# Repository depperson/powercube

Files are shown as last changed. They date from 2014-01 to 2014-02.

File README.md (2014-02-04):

Power Cube
=========

The Power Cube is a modular, universal, self-contained power unit consisting of an engine coupled to a hydraulic pump, providing power from hydraulic fluid at high pressure through quick connect hoses. It is designed to function as a modular and interchangeable power supply for GVCS and other open source technologies.

http://opensourceecology.org/wiki/Power_cube

My goal is to package up all of the necessary documentation to build the Power Cube Version 6.

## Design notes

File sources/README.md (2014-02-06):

Power Cube - Sources
=========

These materials related to the Power Cube were collected from the OSE wiki as a forking point for the project. The version at the time of inclusion was PowerCubeV6. Here are some of the URLs for these files. 

http://opensourceecology.org/wiki/Power_cube

http://opensourceecology.org/wiki/Power_Cube_6/Bill_of_Materials

http://opensourceecology.org/wiki/Power_Cube_6/Manufacturing_Instructions

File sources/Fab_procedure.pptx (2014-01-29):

## 1. Cut Steel

- Tubes, 2 ea: 1/4” x 6” x 12” x 26” long
- Angle iron, 10 ea: 27” per frame diagram
- Angle iron 1/4” x 2” x 2”, 2 ea: 4”, 1 ea: 2”, 2 ea: 8”
- Flat steel, 1/4” x 6”: 1 ea: 6”, 4 ea: 12”
- Flat steel, 1/4” x 8”: 13.5”
- Flat steel 1/8” x 4”: 1 ea: 14”, 2 ea: 1”
- 1 ½" x 2” pipe coupling: cut in half
- 1” engine shaft: cut in half
- 3/4” 11 tooth spline shaft: cut in half

## 2. Fabricate tanks

- Torch, then grind tubes and end plates
- Drill ½” holes for sight gauge
- Install sight gauge
- Weld flanges, pipe coupling and filler neck
- Weld end plates on tanks
- Weld supports for engine & control panel
- Weld battery bracket to fuel tank and solenoid bracket to battery bracket
- Soap bubble test and re-weld if necessary
- Drill smaller 7/16” holes & tap ¼” NPTF
- Mask holes and paint

## 3. Shaft Coupling

- Cut couplings in half
- Preferably: Use lathe to turn down cut ends
- Insert plug into coupling halves
- Clamp and weld
- Let cool standing vertically
- Paint external surfaces

## 4. Weld Frame

- Note: Mitered joints welded on inside and outside
- Begin in one corner, lay two members on flat surface, clamp and weld
- Add third member, clamp and measure – verify parallel with opposing member and weld
- Add forth member, verify alignment and weld
- Complete second rectangle
- Weld hoist points to upper frame members
- Align fifth and sixth members on one rectangle and weld
- Align second rectangle to first, position tanks inside frame and complete frame welds
- Weld expanded steel to hydraulic reservoir
- Weld solenoid bracket to battery bracket
- Paint frame & tank surfaces that will be inaccessible later
- Weld tanks to frame

## 5. Engine/pump mount

- Torch & drill holes in engine & pump plates – verify that holes on engine plate match those on support brackets on tanks
- Weld angle iron to pump plate
- Mount pump on pump plate
- Mount engine on engine plate
- Insert key in shaft coupling and connect to engine
- Slide pump assembly to shaft coupling
- Place 4” spacers between pump & engine plates
- Tack angle iron to engine plate
- Remove spacers and weld
- Remove engine / pump assembly and paint

## 6. Fabricate Control Panel

- Torch, drill, file control panel holes to drawing
- For key switch hole, use switch while filing to test for proper hole size
- Weld throttle bracket to back side & drill bracket
- Paint
- Mount control panel components:
  - Quick couplers
  - Key switch
  - Throttle

## 7. Fabricate Wire Harness

- Cut wire:
  - 2 ea: 10” 2 ga red
  - 1 ea: 12” 2 ga black
- 3/8” copper tubing: 6 ea @ 1 ½”
- Align wires, cut and strip ends appropriately
- Crimp fan connectors on wires
- Crimp circular lug on wire for solenoid
- Crimp pins on wires and insert into connector
- On large gauge wires, begin on ends with single wire – flare ends of copper tubing, insert wire, flatten with hammer and drill
- Proceed to ends with multiple wires – flare, insert, flatten and drill
- Cut heat shrink tubing, install on cables with multiple wires and heat to shrink

## 8. Oil Cooler & Fan

- Put teflon tape onto elbow connector NPT threads
- Screw elbows into oil cooler
- Position oil cooler: elbows up and facing you
- Insert plastic brackets in fan
- Place fan on oil cooler – wires pointing left
- Insert plastic fasteners through oil cooler and plastic fasteners, then secure (use foam pads to protect fins)

## 9. Install Engine / Pump

- Hoist engine / pump
- Attach vibration isolators to supports on tanks – loosely tighten from underneath
- Lower engine into frame until mated with isolators
- With full weight on vibration isolators install and tighten nuts

## 10. Install Oil Cooler & Fan

- Slide oil cooler / fan in place – be careful not to damage cooler fins
- Loosely connect hydraulic hoses to oil cooler elbows
- Test alignment of hydraulic hoses and adjust elbows if necessary
- Install oil cooler/fan to expanded steel using rubber bushings and bolts

## 11. Install Control Panel

- Position control panel
- Connect and tighten hydraulic hoses between oil cooler and control panel
- Connect ¼” hose for “Tank Return” to control panel and tank using hose clamps

## 12. Wire Harness and Battery

- Mount solenoid to bracket
- Insert battery in place
- Plug key switch connector to switch
- Plug in fan connectors
- Connect wire lug to solenoid
- Connect black battery cable to engine bolt and to battery
- Connect red cable to solenoid and engine
- Connect red cable to solenoid, then battery

## 13. Install Suction Plumbing

- Use teflon tape on all NTP threads!
- Install tank strainer in tank
- Install 1” x 4” nipple in strainer
- Install 1” elbow on nipple
- Install suction hose with 2 ea hose clamps

## 14. Install Supply Plumbing

- Use Teflon tape on all NPT threads!
- Connect “long” elbow to pump
- Connect ½” 1' hose between pump elbow and quick connect on control panel – minimize stress on hose
- Install ¾” nipple and filter head to tank – make sure fluid flow is into tank
- Install ¾” elbow in filter head
- Install filter on filter head
- Connect and tighten all ¾” JIC fittings

## 15. Fill With Fluids

## 16.Test

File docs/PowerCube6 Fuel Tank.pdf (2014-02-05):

2/4/2014 | PowerCube6 Fuel Tank - Open Source Ecology
http://opensourceecology.org/wiki/PowerCube6_Fuel_Tank | 1/2

# PowerCube6 Fuel Tank

From Open Source Ecology

Procedure for fabricating the fuel tank. Note that the preparation of the edges for welding is critical, as the welded seams must prevent fuel leaks.

Part List:

Rectangular tube: 1/4" x 6" x 12" - 26" long [2] Flat Steel: 1/4" x 6" x 12"Weld-in Fuel Filler Neck and Cap Smallsheet plastic Fuel Pickup Adapter 1/4" rubber hose Soapy water

1. Grind the 1/4" x 6" x 12" plates, rounding the corners to 1/2" radius and beveling the edges for welding.
2. Grind the 1/2" x 6" x 12" Tube, beveling the edges for welding.
3. Cut the 7/16" and 2" holes in the tube as shown. The larger hole may be cut with an Oxy/Acetylene torch, then smoothed with a grinder. Note that the inside of the hole should be 2" in diameter.
4. Weld the plates to the ends of the tube
5. Tap the 7/16" hole for 1/4" NPTF threads, smooth the welds with the grinder.
6. Pressure test the tank by covering the filler neck with a plastic sheet, then securing the cap. Secure the smaller hole with a the fuel pickup and some 1/4" hose on the hose barb. Apply compressed air to the end of the rubber hose to pressurize the tank, then apply soapy water to all welds and check for bubbles.
7. Mark any bubbling spots with a felt-tip marker and re-weld
8. Re-test the tank and re-weld as necessary to stop all leaks

2/4/2014 | PowerCube6 Fuel Tank - Open Source Ecology

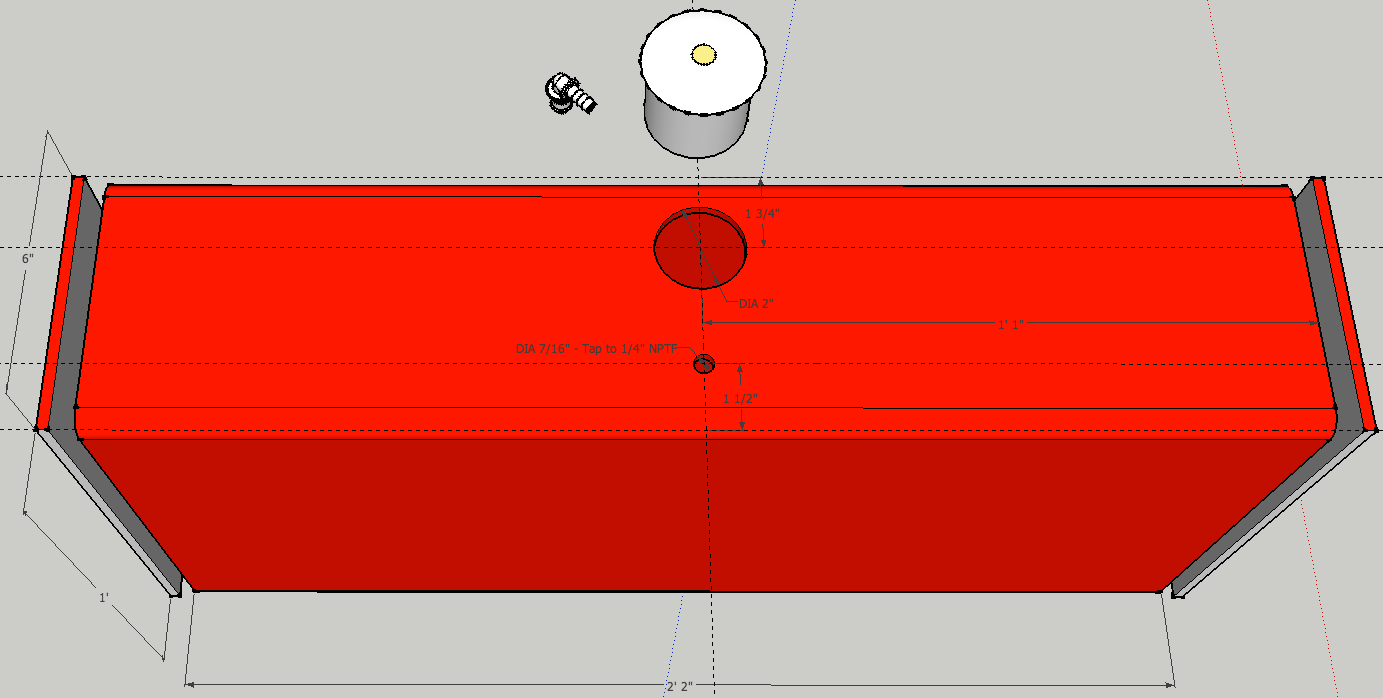
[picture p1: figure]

http://opensourceecology.org/wiki/PowerCube6_Fuel_Tank | 2/2

Retrieved from "http://opensourceecology.org/w/index.php?title=PowerCube6_Fuel_Tank&oldid=71505"

This page was last modified on 21 August 2012, at 02:56.
Content is available under CreativeCommons by-sa3.0. (http://opensourceecology.org/wiki/Copyright)

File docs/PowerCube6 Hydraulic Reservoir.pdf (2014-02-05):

2/4/2014 | PowerCube6 Hydraulic Reservoir - Open Source Ecology
http://opensourceecology.org/wiki/PowerCube6_Hydraulic_Reservoir | 1/2

# PowerCube6 Hydraulic Reservoir

From Open Source Ecology

Procedure for fabricating the hydraulic reservoir. Note that the preparation of the edges for welding is critical, as the welded seams must prevent fluid leaks.

Part List:

1/4" x 6" x 12" - 26"Rectangular tube
[2] 1/4" x 6" x 12" Flat Steel
[2] 3/4" NPTF weld-in flange
3/4" NPTM plastic tank breather
1 1/2" NPTF x 3" union
Hydraulic tank thermometer and sight gauge
[2] 1/4" NPTM plug - Galvanized
[2] 3/4" NPTM plug - PVC
1 1/2" NPTM plug - PVC
Schrader air valve
Soapy water

Procedure:

1. Grind the 1/4" x 6" x 12" plates, rounding the corners to 1/2" radius and beveling the edges for welding.
2. Grind the 1/2" x 6" x 12" Tube, beveling the edges for welding.
3. Cut the 7/16", 1 7/16" and 2" holes in the tube as shown. The larger holes may be cut with an Oxy/Acetylene torch, then smoothed with a grinder.
4. Tap threads in the two smaller holes with a 1/4" NPTF tap
5. Weld the three flanges to the tank
6. Weld the "front" plate (ie: the one near the oilfilter) to the end of the tube
7. Drill the two 1/2" holes for site gauge and securely install the site gauge
8. Tap the 7/16" hole for 1/4" NPTF threads, smooth the welds with the grinder.
9. Pressure test the tank by covering the filler neck with a plastic sheet, then securing the cap. Secure the smaller hole with a the fuel pickup and some 1/4" hose on the hose barb. Apply compressed air to the end of the rubber hose to pressurize the tank, then apply soapy water to all welds and check for bubbles.
10. Mark any bubbling spots with a felt-tip marker and re-weld
11. Re-test the tank and re-weld as necessary to stop all leaks

2/4/2014 | PowerCube6 Hydraulic Reservoir - Open Source Ecology

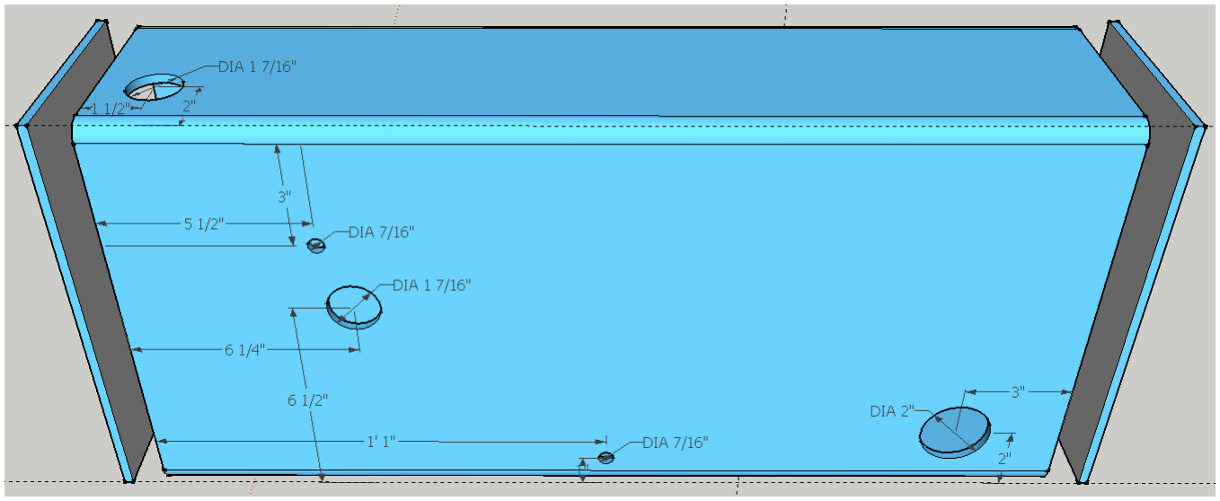
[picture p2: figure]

http://opensourceecology.org/wiki/PowerCube6_Hydraulic_Reservoir | 2/2

Retrieved from "http://opensourceecology.org/w/index.php?title=PowerCube6_Hydraulic_Reservoir&oldid=71588"

This page was last modified on 22 August 2012, at 14:56.
Content is available under CreativeCommons by-sa3.0. (http://opensourceecology.org/wiki/Copyright)

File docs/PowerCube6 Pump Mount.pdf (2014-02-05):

2/4/2014 | PowerCube6 Pump Mount - Open Source Ecology

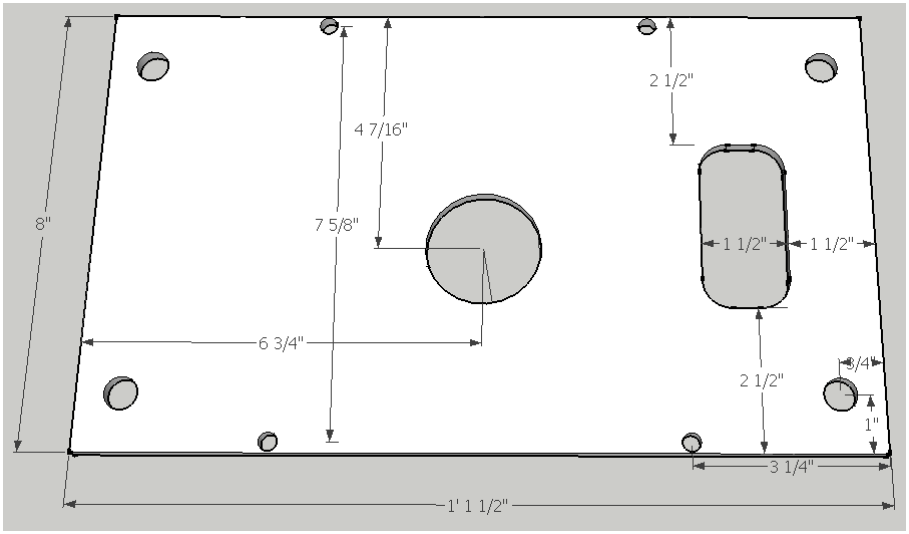
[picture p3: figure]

http://opensourceecology.org/wiki/PowerCube6_Pump_Mount | 1/5

# PowerCube6 Pump Mount

From Open Source Ecology

## Engine Mounting Plates

¼” x 8” x 13.5” Plate

¼” x 6” x 6” Plate

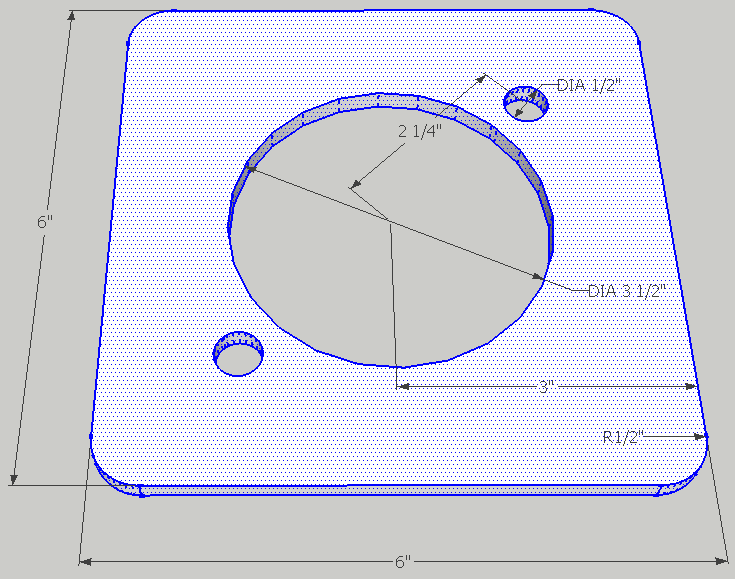
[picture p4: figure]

¼” x 2” x 2” x 5” Angle (2 ea)

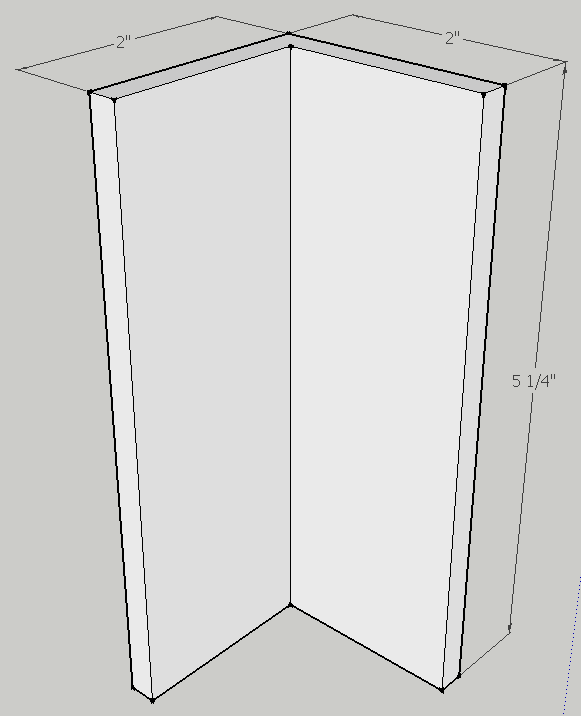
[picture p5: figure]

## Engine / Pump Mount Assembly

Align the two 1/4" x 2" x 2" anglt iron pieces on the pump plate as shown below and weld securely.

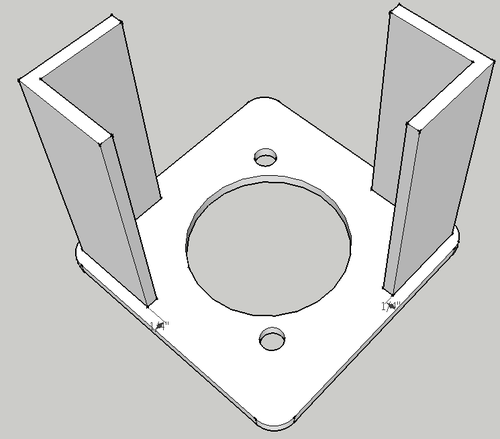
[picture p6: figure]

Mount the engine to the engine plate using [4] 5/16” x 2” bolts and [4] rubber vibration mounts.

Slide the shaft coupling onto the engine shaft and secure the hex screw.

Mount the pump onto the pump plate and secure with [2] 7/16" x 1 1/2" bolts.

Slide the splined pump shaft into the shaft coupling so the angle touches the engine plate and is oriented as shown.

See the following video for details:

Examine the engine shaft – it should be 2” long. If longer, cut the shaft to extend no more than 2” from the case. This length is necessary for the coupling. Put the larger keystock in the engine shaft and slide the shaft coupling on the engine shaft and tighten the allen screws to hold it in place.

Retrieved from "http://opensourceecology.org/w/index.php?title=PowerCube6_Pump_Mount&oldid=71278"

This page was last modified on 18 August 2012, at 06:29.
Content is available under CreativeCommons by-sa3.0. (http://opensourceecology.org/wiki/Copyright)

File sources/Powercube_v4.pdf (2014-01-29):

Power Cube | Open Source Ecology | Page 1

# Power Cube

Version 4

Contents

## Table of Contents

Introduction

The Power Cube is an universal, self-contained power unit that consists of an engine coupled to a hydraulic pump for providing power in the form of hydraulic fluid at high pressure. It connects via quick couplers and quick-connect hydraulic hoses to devices such as:

- LifeTrac
- CEB Press
- Sawmill

◦

This document provides information for building and using a Power Cube as part of the Open Source Ecology (OSE) project.

Check the OSE website for updates to this document:

http://opensourceecology.org/wiki/File:Powercube.odt

Bill Of Materials

Discrete parts

Name | Qty | Dimensions | Manufacturer /
Retailer | Part No.
Engine | 1 | 28 HP | Briggs & Stratton | 49M777 Series
Solid Shaft Coupling | 1 | 1 1/8” x 5/8” | Sweiger Shop | Custom
Hydraulic Pump | 1 | 0.976 cu in | SurplusCenter.com | 9-1766-B
SAE 10M x 3/4” NPTF Adapter | 1 | 3/4” NPTM | SurplusCenter.com | 9-6405-10-12
3/4" NPTF Return Filter & Head | 1 | 20 GPM | SurplusCenter.com | 9-059
14 GPM Hydraulic Tank Strainer | 1 | 1 1/2” F x 1” M SurplusCenter.com | 9-7290-100
3/4" NPTM TO 3/4" NPTM 90
Elbow | 1 | ¾” | SurplusCenter.com | 9-5500-10-12
JIC 12M x 3/4 NPTM 90 ELBOW | 1 | 12M x 3/4” | SurplusCenter.com | 9-2501-12-12
3/4" Quick Coupler S40-6 F/F | 1 | 3/4” | SurplusCenter.com | 928-C
1/4" NPT Quick Coupler S40-2 | 1 | 1/4” | SurplusCenter.com | 9-6314
1/4 NPTM TO 3/4 NPTF
ADAPTER | 1 | 1/4” x 3/4” NPT SurplusCenter.com | 9-5405-12
NPT Weld-In Tank Flange | 1 | 1 1/2” | SurplusCenter.com | 9-7843-24
NPT Weld-In Tank Flange | 2 | 3/4” | SurplusCenter.com | 9-7843-12
NPT Weld-In Tank Flange | 1 | ¼” | SurplusCenter.com | 9-7843-4
Hose barb | 1 | ¼" NPTM x 1/4" SurplusCenter.com | 455-AA
1" Hose Barb to SAE 12M
Adapter | 1 | 1” Hose x SAE
| | 12M | SurplusCenter.com | 9-4604-16-12
1" Hose Barb to 1" NPTM
Adapter | 1 | 1” x 1” NPTM SurplusCenter.com | 9-4404-16-16
Hydraulic Suction Hose | 1 | 3' | SurplusCenter.com | 9-1279
Hydraulic Oil Cooler | 1 | Approx 12” x 15” SweigerShop.com | Custom
JIC 12F X JIC 12F 3000 PSI
HYD HOSE | 1 | 3/4” x 12” | SurplusCenter.com | 951-2212
3/4" NPT PLASTIC TANK
BREATHER | 1 | 3/4” | SurplusCenter.com | 9-7957-12
3/4" X 3/4" X 3/4" NPTF TEE | 1 | 3/4" x 3/4" x 3/4" SurplusCenter.com | 9-5605-12-12-12
3/4" NPT HEX NIPPLE | 4 | 3/4” | SurplusCenter.com | 9-5404-12-12
JIC 12M x 3/4" NPTM 90 Elbow | 1 | 3/4” | SurplusCenter.com | 9-2501-12-12

Name | Qty | Dimensions | Manufacturer /
| | | Retailer | Part No.
JIC 12M x JIC 12M UNION | 1 | JIM 12M | SurplusCenter.com | 9-2404-12-12
Solenoid | 1 | | SurplusCenter.com | 11-1108
12 Volt radiator fan | 1 | 12” - 14” | Auto Part
Rubber Fuel Line | 1 | 24” | Auto Part
Battery | 1 | 5" x 7.5" x 7.5" Walmart | UIP-7
Galvanized Nipple | 4 | 1” | Home Depot | 64310
Galvanized Elbow | 2 | 1” | Home Depot | 510-003HN
Galvanized Washer | 4 | 2 ½” | ?? | ??
Galvanized Round | 2 | 2” | ?? | ??
Teflon Tape | 1 roll | ½” wide | Home Depot | ??
1 Gauge Wire | 30” | 1 gauge | Auto Part | ??
1 gauge ring connector
- or -
Copper tubing | 6
- or -
| 9” | 1 gauge
- or -
| | 3/8” | Auto Part | ??
Ignition Switch | 1
12 V Fan Switch | 1
Bolt (Angle iron attach) | 4 | ½” x 2” x 12 TPI
Nut (Angle iron attach) | 4 | ½” x 12 TPI
Washer flat | 8 | ½”
Bolt (Engine mount) | 4 | ¼” x 2” 16 TPI
Nut (Engine mount) | 4 | ¼” x 16 TPI
Bolt (Hydraulic motor mount) | 4 | ¾” x 3.5” x 12 TPI
Nut (Hydraulic motor mount) | 8 | ¾” 12 TPI
Lock washer (Hydraulic motor mount) | 4 | ¾”
Nut (Fan mount) | 4
Bolt (Fan mount) | 4
Bolt (Solenoid mount) | 2
Tractor Enamel: Glossy Black | 1 | pint

Steel
Type | Thickness | Width | Total Length (rounded up)
Angle | ¼" | 2" x 2” 408" (34 ft)
Angle | 1/8” | 2” x 2” 6”
Plate | ¼" | 8" | 38" (4ft)

Plate | ¼” | 2” | 120” (10 ft)
Plate | ¼" | 6" | 24" (2 ft)
Plate | 3/8” | 4” | 54” (5 ft)
Tube | ¼” | 4” x 8” 14 ½” (2 ft)
Tube | ¼” | 6” x 12” 27 ½” (Hydraulic reservoir)
Tube | 1/8” | 4” | 2” | (black pipe)
Tube | 1/8” | 1 9/16” 12” | (Galvanized Muffler Pipe)
Tube | 1/8” | 6 cm | 14” | (Galvanized Muffler Pipe)
Expanded Steel | 13 gauge | 12” | 22” | (Oil cooler grill)

Subassembly Fabrication
Many of the items listed in the Bill Of Materials require preparation before use in assembly of the Power Cube. This includes drilling and cutting steel up to 3/8” in thickness. These are the parts for assembling a Power Cube. Parts without special detail are not illustrated.
1. Engine and Hydraulic Pump mounts
a) ¼” x 8” x 12” Plate
b) ¼” x 8” x 9” Plate
c) ¼” x 2” x 2” x 8” Angle
d) ¼” x 2” x 2” x 29” Angle
e) ¼” x 8” x 8” Plate

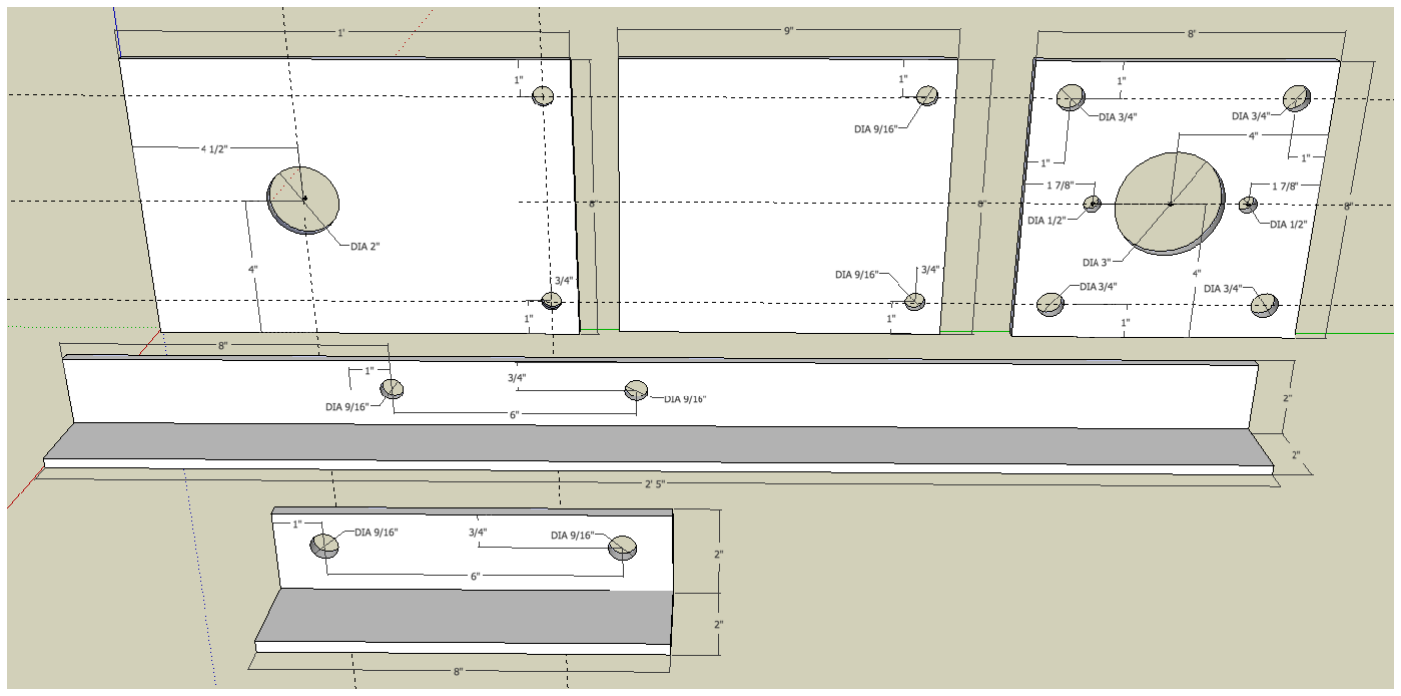
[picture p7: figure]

2. Quick attach mounts
a) [2] 3/8” x 4” x 27” Plates

3. Fuel tank
a) [2] ¼” x 4” x 8” Plates
b) 4” x 8” x 14 ½” Tube
c) ¼” x 2” x 24” Plate
d) All welds assembling the tank must be quality welds, as they must not leak. Be careful not to “over weld” the tank to the mount.
e) Clean the inside of the ¼” x 4” x 8” tube and the two ¼” x 4” x 8” plates – anything left on these surfaces will end up in the gasoline and could clog the engine when started. Tack and weld the plates on each end of the tube, taking care to orient the top plate with the filler hole as shown in the diagram below.
f) Weld the 1/4” tank flange to the hole in the side of the tank tube.

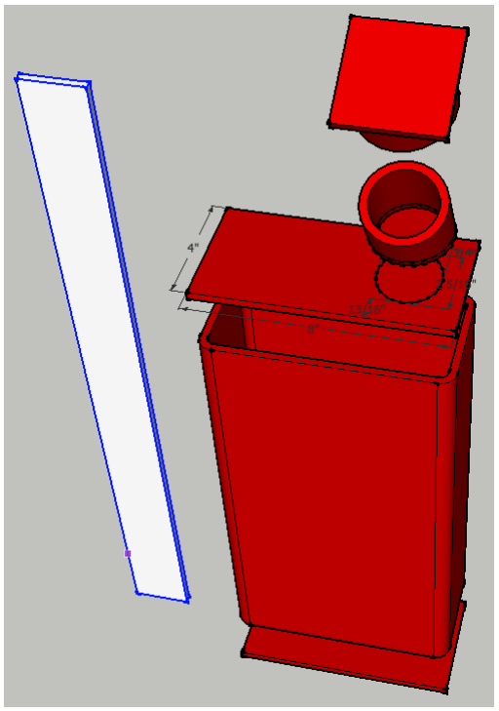
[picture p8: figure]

4. Oil Cooler Mount
a) [2] ¼” x 2” x 24” Plates
b) [2] ¼” x 2” x 1” Plates
c) [2] ¼” x 2” x 22” Plates (Note: the holes in these plates may need adjustment based on oil cooler mounting holes)
5. Key Switches and Choke Brackets
a) [3] 1/8” x 2” x 2” x 2” Angle

6. Electrical cables
a) The connectors can be purchased from an auto parts store – be aware that they usually require a crimper to attach to the cables. Alternatively, 3/8” copper tubing can be used in 1 ½” long pieces instead. Strip 1 ½” insulation from the cable, fully insert fully into 1 ½” copper tube, flatten end with a hammer and drill hole.
b) [2] 1 gauge cables: 11” (verify length first!)
c) 1 gauge cable: 8 ½” (verify length first!)

7. Battery Mounts
a) [2] ¼” x 2” x 2” x 4 3/4” Angle
b) [2] ¼” x 2” x 5/8” Plate

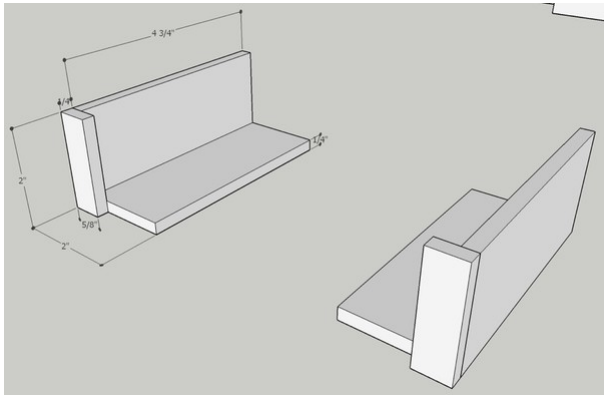
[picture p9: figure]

8. Oil filter Assembly
a) Assemble as shown, using teflon tape on all threaded components.

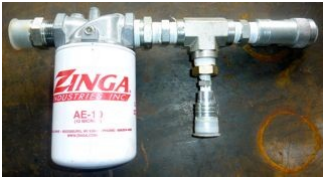
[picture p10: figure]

b) The parts for this are (from left to right):
- 1” nipple
- Oil filter and header
- 1” to ¾” reducer

- ¾” nipple
- ¾” T adapter
- ¾” to 3/8” recucer
- ¼” quick connect
- ¾” T adapter
- ¾” quick connect
9. Hydraulic reservoir
a) [2] ¼” x 6” x 12” Plates
b) ¼” x 6” x 12” x 27 ½” Tube
c) All welds assembling the reservoir must be quality welds that do not leak. Be careful not to “over weld” the reservoir.
d) Clean the inside of the tube and the two end plates – anything on these surfaces will end up in the hydraulic oil and could damage the pump or cylinders.
e) Tack and weld the 6” x 12” plates to both ends of the 6” x 12” tube. Pay attention to the orientation of the plate with the filler hole and the side of the tube with other holes – see the diagram below.

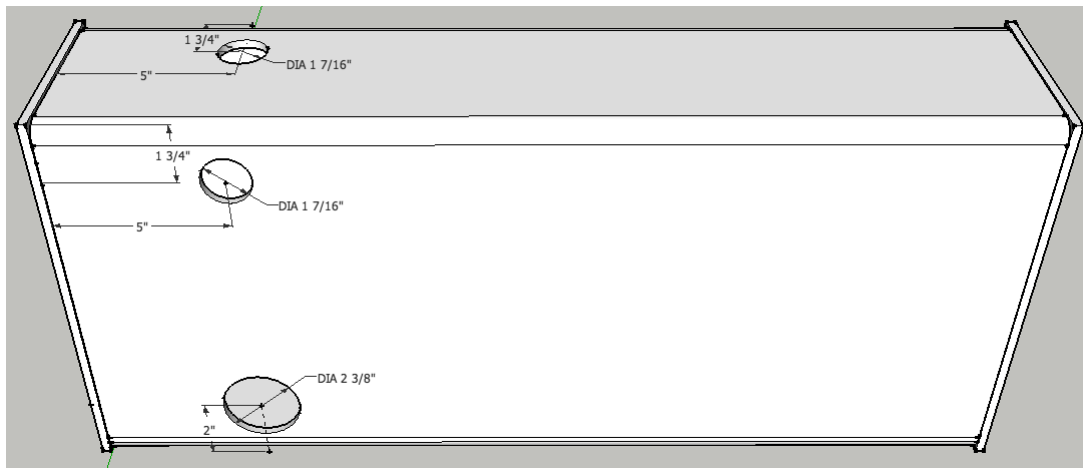
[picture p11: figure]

f) Tack and weld the strainer extension tube to the tank, centered around the strainer hole.
g) Insert the strainer into the flange and insert it into the strainer extension tube – verify that it slides without binding or bottoming and that the flange is flush with the end of the tube.

Remove the strainer from the flange, then tack and weld the flange to the tank.

CAUTION: Keep the strainer away from the welding, as its thin wires burn easily.
h) Install the suction strainer and the hose barb with the hose barb pointing toward the hydraulic pump (Photo below is for assembly, hose barb is oriented differently).

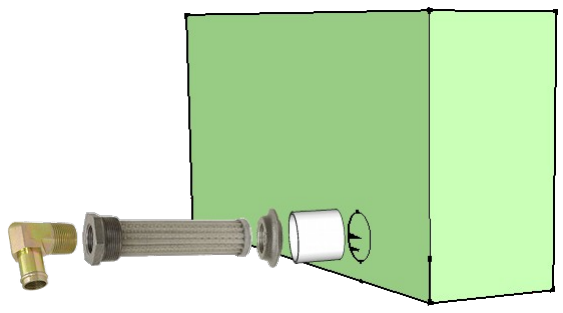
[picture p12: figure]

Assembly
Power Cube assembly requires all the parts listed in the Bill Of Materials to be available and prepared as detailed in the “Fabrication” section (above). Assembly requires a welder (electric or torch) capable of welding metal 3/8” thick.
An optional jig can be used to aid in assembly. See Appendix 1 for details.
1. Frame
a) Top / Bottom Rectangles

Position two ¼” x 2” x 2” x 29” pieces angle iron on top of two 27” angle pieces as shown below. Check that all joints are square, then tack and weld joints.

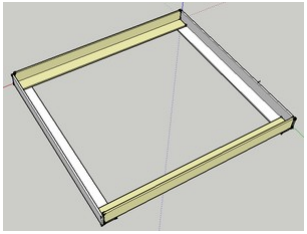
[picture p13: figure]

b) With one welded rectangle on the bottom, position two 24” pieces outside corner joints as shown below. Check that the angles are square, then tack and weld. Note: The optional jig makes this much easier and accurate. Repeat the prior procedure and this one for another half of the frame assembly.

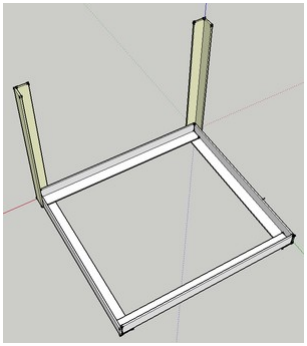
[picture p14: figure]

c) Position the second rectangle as shown below, then tack and weld. Inspect all corners to verify secure welds.

2. Gas tank
a) Screw the 1/4" hose barb into the 1/4 NPT flange welded into the gas tank.
b) Perform a “soap bubble” test on the tank. Securely cover the larger hole (use something like strong tape), pressurize the tank using the smaller hole and cover the tank surface with soapy water. Look closely for new bubbles, mark any leaks and re-weld securely. Repeat soap bubble test if re-welded.
c) Tack and weld the gas tank mount (¼” x 2” x 24” plate) to the frame. Position it so the gas tank is 1" from the nearest vertical angle iron support.
d) Tack and weld the gas tank to the gas tank mount as shown below.

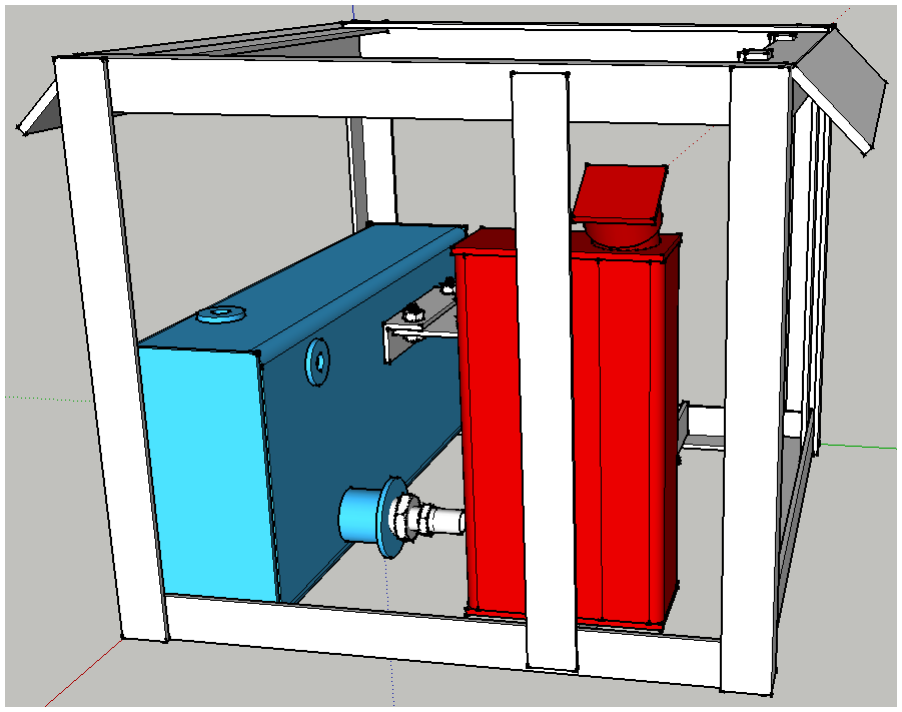
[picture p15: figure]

3. Hydraulic reservoir

The reservoir should already be pre-assembled and ready for installation.
a) Perform a “soap bubble” test on the tank by securely covering the larger hole (use something like strong tape), pressurizing the tank using the smaller hole and cover the tank surface with soapy water. Mark any leaks and re-weld securely. Repeat soap bubble test if re-welded.

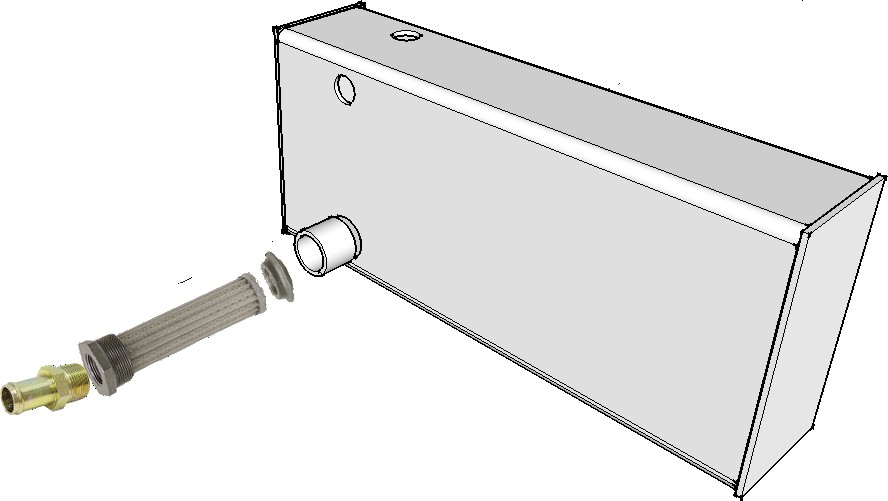
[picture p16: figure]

b) Secure the hydraulic tank to the frame with clamps, then weld it with 4 x 1” welds. The tank is ¼” and it can be easily damaged by over-heating. Spacers may be needed on the sides near the top to keep everything snug.

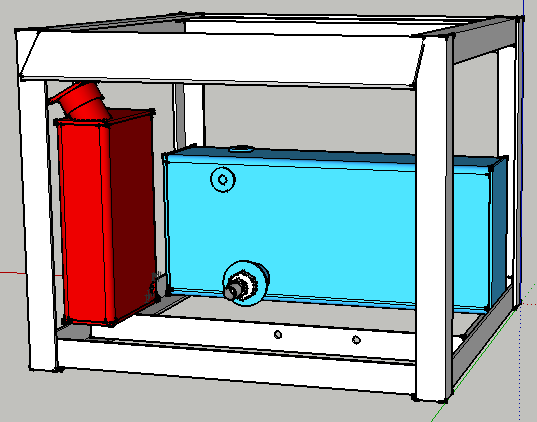
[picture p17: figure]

4. Engine Mounts and Hydraulic Pump Mount
a) Bolt the ¼” x 2” x 2” x 8” plate to the ¼” x 2” x 2” x 29” angle as shown using 1/2” x 2” bolts:

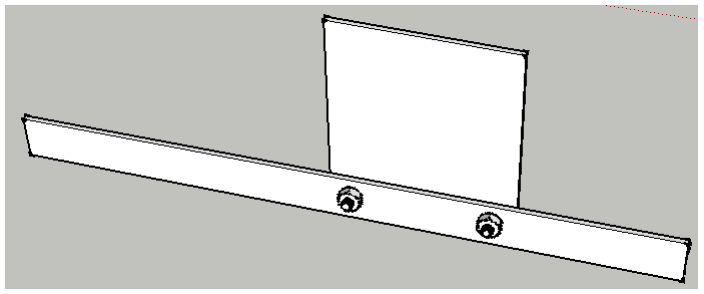
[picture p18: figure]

b) Bolt the ¼” x 8” x 12” plate to the 8" angle as shown using 1/2” x 2” bolts:

c) Align the plate edges and secure at 90 degree angle and weld. We use welding magnets to hold the plates at 90 degrees:

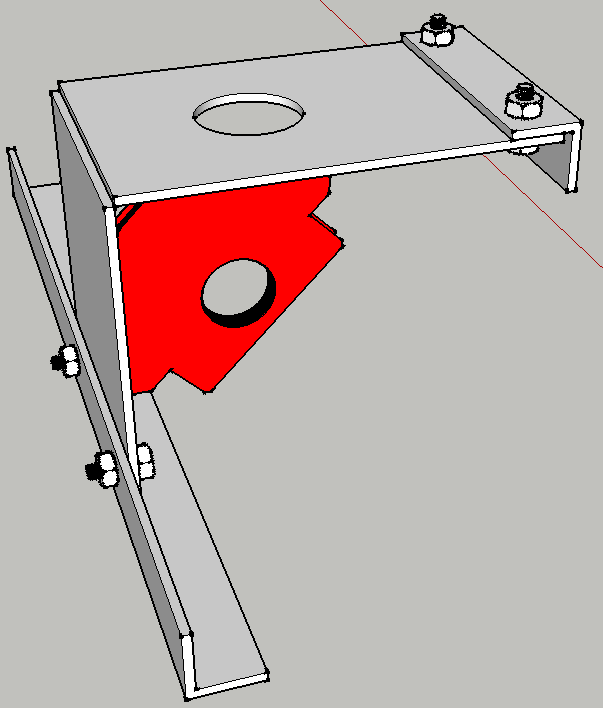
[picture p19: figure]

d) Mount the engine to the engine plate using [4] 5/16” x 2” bolts. The method for mounting may depend on your engine. See the following video for details:

http://youtu.be/DO6wbwOjWNA

e) Examine the engine shaft – it should be 2” long. If longer, cut the shaft to extend no more than 2” from the case. This length is necessary for the coupling. Put the larger keystock in the engine shaft and slide the shaft coupling on the engine shaft and tighten the allen screws to hold it in place.

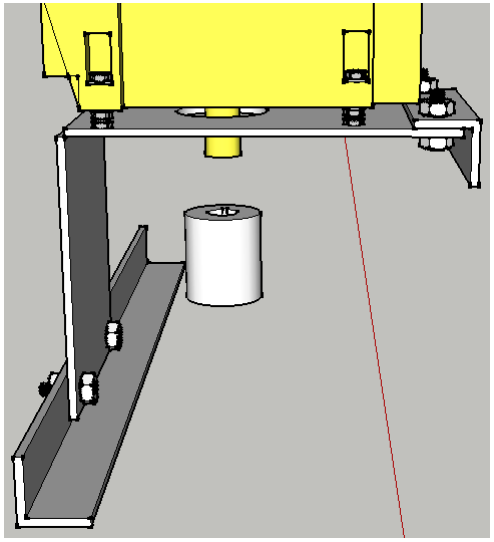
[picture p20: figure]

f) Assemble the 8” x 8” pump plate as shown with [4] ¾” x 3.5” bolts and [8] 3/4” nuts, [8] washers and [4] lockwashers. Tighten the nuts to hold the plate firmly:

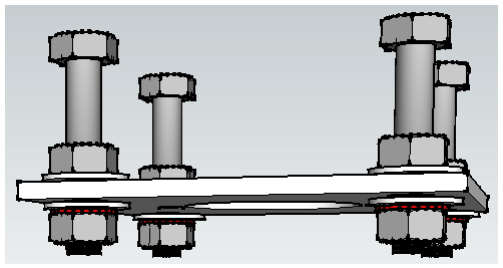
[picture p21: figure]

g) Mount the pump to the pump plate using [2] 7/16 bolts, nuts and washers:

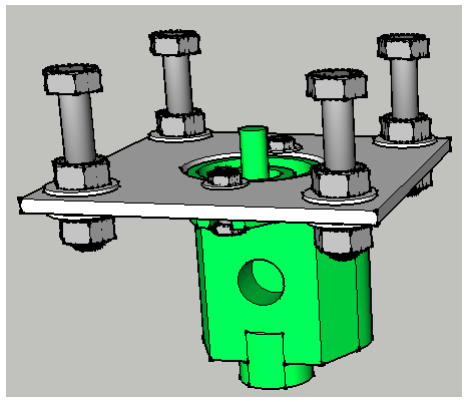
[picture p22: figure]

h) Make sure the key is in the pump shaft and slide the pump shaft into the bottom of the shaft coupling and tighten its allen screws. The bolt heads should just be touching the bottom of the engine plate. Tack and weld the bolt heads to the engine plate.

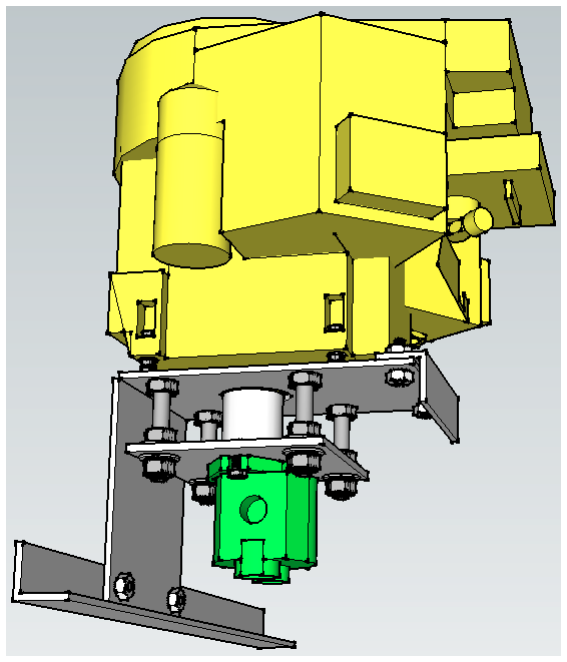
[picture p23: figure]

i) Lower the engine/pump assembly into the frame. Adjust it so the engine plate is parallel with the frame and weld the 8” angle iron to the reservoir and the 29” angle iron to the frame.

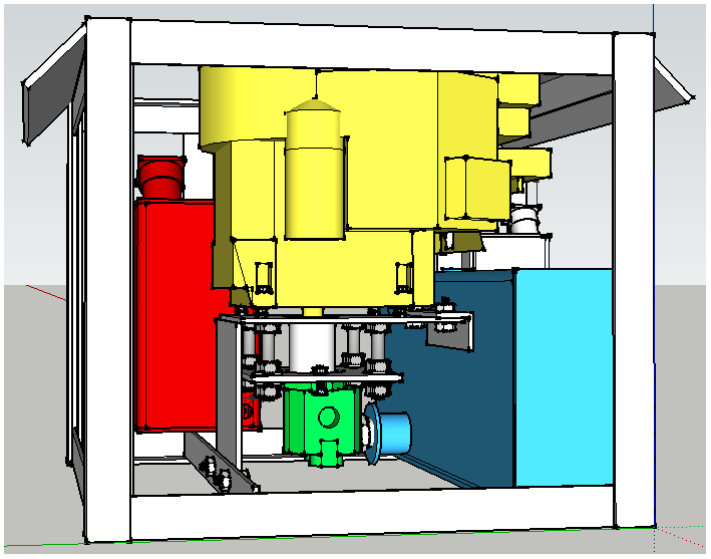
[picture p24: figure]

5. Battery mount
a) Weld the ¼” x 2” x 5/8” plates to the ends of the ¼” x 2” x 2” x 4 3/4” plates as shown below.
b) Weld the two mounts to the angle iron and tank to form a rectangle for the battery as shown below.


c) After the mount has cooled, lower the battery into the rectangle to verify a proper fit.
6. Oil cooler and fan mounts
a) Position the two ¼” x 2” x 22” plates to the outside of the frame, adjust so the oil cooler mounting bolts match the holes in the plates and is positioned as in the diagram below. Tack and weld the mounts in to the frame. Verify that the oil cooler bolts match the holes in the mounts.


b) Use the mounting holes in the fan shroud and the oil cooler width for positioning the mounting plates as shown in the diagram below. Position the four ¼” x 2” x 1” plates, then tack and weld. Position the two ¼” x 2” x 24” plates against the 1” plates, then tack and weld. Place the fan on the supports and mark the mounts with bolt hole positions. Place the bolt heads against the fan mounting plate and weld in place. Verify that the bolts match the holes in the fan. Inside the frame, adjust the fan position to position fan shroud ¼” from oil cooler fins. Be careful with radiator as the delicate fins are easily bent and damaged.
c) Place the 9 gauge x 12” x 22” expanded steel grill in front of the oil cooler mounting plates, positioned to cover the entire oil cooler and check if any holes are necessary to secure with oil cooler mounting bolts.


7. Screw the filter assembly into the flange on the side of the hydraulic reservoir.


8. Connect the 1” suction hose between the strainer and the pump intake.
9. Connect a male ¾” quick connect hydraulic coupler to the pump output.
10. Connect a female ¾” to ¾” elbow to the cooler port nearest the battery cage.
11. Connect one end of the ¾” x 1' hydraulic hose to the second cooler port, then connect the other end of the ¾” x 1' hydraulic hose to filter assembly.


12. Weld the 1/8” x 2” x2” x 2” angle brackets to the frame in the positions shown below. Pay special attention to the hole sizes, as the bracket for the choke has a smaller hole.
<image>
13. Weld the solenoid mounting bolts to the hydraulic reservoir as shown below.
<image>
14. Wire the switches.
15. Fix the throttle control, connect to throttle plate.

User Guide
This section is intended for the end user of the Power Cube.
1. Caution
a) Weight
b) Hydraulic hazards
c) Ventilation
2. Mounting
a) Quick attach connector
3. Initial startup and testing
a) Initial Setup
- Gasoline
- Hydraulic Fluid
- Battery Connection
b) Startup
c) Hydraulic Test
4. Routine use
5. Maintenance
a) Engine Oil
b) Hydraulic Fluid
6. Troubleshooting
a) Engine won't start
b) Loud noise
c) No hydraulic power

Appendix

Frame Assembly Jig

The welding “jig” in the image below is helpful to insure square angles while assembling the Power Cube. It is very useful if building multiple Power Cubes.


Note the corner holes that provide access for welding:

Materials List

- ¼” x 2” x 2” Angle Iron: 14'

- ½" Rebar: 7' 2”

Cut List
Type | Length | Dimensions | Quantity | Color
Angle | 22" | ¼” x 2 x 2" | 2 | (red)
Angle | 26" | ¼” x 2” x 2” | 2 | (yellow)
Angle | 29" | ¼” x 2" x 2 | 2 | (green)
Rebar | 30.5" | ½" | 1
Rebar | 27" | ½" | 2

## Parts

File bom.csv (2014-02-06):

Line | Qty | Supplier | Part# | Description | Quote | Purchase Price | Purchase date | Notes
1 | 2 | surpluscenter.com | 9-7843-12 | 3/4" NPT FORGED WELD-IN TANK FLANGE | $2.75
2 | 1 | surpluscenter.com | 9-7287-10 | 10" RESERVOIR SIGHT LEVEL GAUGE W/TH | $20.99
3 | 1 | surpluscenter.com | 9-5404-12-12 | 3/4 NPT HEX NIPPLE | $2.65
4 | 1 | surpluscenter.com | 9-4604-16-16 | 1" HOSEBARB TO SAE 16M ADAPTER 4604-1 | $7.19
5 | 1 | surpluscenter.com | 9-4404-16-16 | 1" HOSEBARB TO 1 NPTM ADAPTER 4404-16-16 | $6
6 | 1 | surpluscenter.com | 455-AA | 1/4" HOSE BARB X 1/4" NPTM 4244-4-4 | $1.25
7 | 2 | surpluscenter.com | 28-1478 | 1/4" NPTM X 1/4" I.D. HOSE BARB STEEL ELBOW | $0.49
8 | 1 | surpluscenter.com | 9-059 | 3/4" NPT 20 GPM FA1200-10 RETURN FILTER | $17.95
9 | 1 | surpluscenter.com | 9-7290-100 | 1-1/2" NPTM TO 1" NPTF 14 GPM TANK STRAINER | $19.95
10 | 4 | surpluscenter.com | 9-2501-12-12 | JIC 12M x 3/4 NPTM 90 ELBOW | $5.59
11 | 1 | surpluscenter.com | 951-2230 | 3/4" X 30" JIC 12F X JIC 12F 3000 PSI HYD HOSE | $21
12 | 1 | surpluscenter.com | 951-2224 | 3/4" X 24" JIC 12F X JIC 12F 3000 PSI HYD HOSE | $19
13 | 1 | surpluscenter.com | 9-6801-L-10-10 | JIC 10M TO SAE 10M LONG 90 ELBOW | $6
14 | 1 | surpluscenter.com | 9-2501-10-12 | JIC 10M x 3/4 NPTM 90 ELBOW | $5.39
15 | 1 | surpluscenter.com | 941-2212 | 1/2" X 12" JIC 10F X JIC 10F 3500 PSI HYD HOSE | $10
16 | 1 | surpluscenter.com | 9-4848-E | 0.98 cu in HYDRECO HMP3 162025A2 HYD | $105.99
17 | 1 | surpluscenter.com | 928-C | 3/4" QUICK COUPLER S40-6 F/F | $25.95
18 | 1 | surpluscenter.com | 9-6314 | 1/4" NPT QUICK COUPLER S40-2 | $15.95
19 | 1 | surpluscenter.com | 11-1108 | 12 VDC SPST RELAY STARTER SOLENOID R | $6.95
20 | 1 | surpluscenter.com | 1-2849 | 49" THROTTLE CONTROL CABLE W/ T-LEVER | $4.95
21 | 1 | surpluscenter.com | 9-7957-12 | 3/4" NPT PLASTIC TANK BREATHER | $4.49
22 | 1 | surpluscenter.com | 1-2985 | 3/4"-11 TOOTH SPLINED COUPLING | $15.95
23 | 1 | surpluscenter.com | 1-1563-E | 1" SHAFT COUPLER | $11.95
24 | 1 | surpluscenter.com | 1-1563-F | 1-1/8" SHAFT COUPLER | $14.95
25 | 5 | surpluscenter.com | 9-1279 | 1" HYD SUCTION/RETURN HOSE (SOLD BY THE FOOT) | $25
26 | 1 | Amazon.com | 430-538 | Stens 430-538 Starter Switch | $11.11
27 | 1 | Amazon.com | B001OK9ZDI | Universal Wiring Harness | $8.99
28 | 1 | Amazon.com | 3653 | Hayden Automotive 3653 Adjustable Thermostatic Fan Control | $16.38
29 | 1 | Amazon.com | 1268 | Hayden Automotive 1268 Heavy Duty Oil Cooler | $122.83
30 | 1 | Amazon.com | PC-2052 | PROCOMP 12" RADIATOR FAN CURVED 12 VOLT | $17.95
31 | 1 | Amazon.com | 13001 | Derale 13001 Plastic Rod Mounting Kit | $6.25
32 | 4 | Grainger.com | 2NPA8 | Vibration Isolator, 80 Lb Max, 5/16-18 | $3.11
33 | 1 | DigiKey.com | A1456-ND | CONN PLUG 6POS 94V-2 UNI-MATE | $0.29
34 | 3 | DigiKey.com | A97893CT-ND | CONN PIN 20-14AWG TIN UMNL | $0.1
35 | 1 | Auto Parts Store |  | 1 1/2" muffler pipe clamp | $2.95
36 | 1 | Auto Parts Store |  | 1/4" key stock | $1
37 | 1 | Coyote Gear |  | Fuel filler neck with Scalloped Vented Steel Cap | $18.95
38 | 1 | Wal-Mart | UIP-7 | Battery | $45
39 | 1 | Local | Expanded steel | 1/8" x 14" x 26" | $27
40 | 1 | Local | Flat Iron | 1/8" x 4" x 18" | $15
41 | 1 | Local | Flat Iron | 1/4" x 6" x 5' | $36
42 | 1 | Local | Angle Iron | 1/4" x 2" x 2" x 32' | $70
43 | 1 | Local | Flat Iron | 1/4" x 8" x 13 1/2" | $54
44 | 1 | Local | Flat Iron | 2" x 2" x 6'
45 | 1 | Local | Rectangular Tube | 1/4" x 6" x 12" x 44"
46 | 1 | Local | Flat Iron | 3/8" x 4" x 52" | $35
47 | 4 | Hardware Store |  | Bolt: 1/4" x 3/4"
48 | 8 | Hardware Store |  | Bolt: 5/16" x 1 1/2"
49 | 2 | Hardware Store |  | Bolt: 3/8" x 1 1/2"
50 | 4 | Hardware Store |  | Nylon lock nut: 1/4"
51 | 8 | Hardware Store |  | Nylon lock nut: 5/16"
52 | 2 | Hardware Store |  | Nylon lock nut: 3/8"
53 | 4 | Hardware Store |  | Washer: 1/4"
54 | 8 | Hardware Store |  | Washer: 5/16"
55 | 2 | Hardware Store |  | Washer: 3/8"
56 | 1 | Hardware Store |  | Compression Coupling 1/4" NPTF X 3/8" TUBING | $3
57 | 1 | Hardware Store |  | Copper Tubing: 3/8" x 9" | $10
58 | 1 | Hardware Store |  | 1 1/2" NPTF Pipe coupling 2" long | $4
59 | 1 | Hardware Store |  | 1" Galvanized 3" nipple | $3
60 | 1 | Hardware Store |  | Galvanized Pipe 90 degree Elbow: 1" NPTF | $3
61 | 1 | Hardware Store |  | Hydraulic Tape | $3
62 | 20" | Hardware Store |  | 1/4" Rubber Fuel line | $3
63 | 20" | Hardware Store |  | 2 Gauge Wire, Red | $15
64 | 12" | Hardware Store |  | 2 Gauge Wire, Black | $8
65 | 1 | Hardware Store |  | Rustoleum Black Paint (quart) | $15
66 | 4 | Hardware Store |  | 1/4" Hose Clamp | $0.5
67 | 2 | Hardware Store |  | 1 1/2" Hose Clamp | $1
68 | 1 | SmallEngineSuppliers.com | MUF0626R | Briggs & Stratton Muffler | $72.95
69 | 1 | SmallEngineSuppliers.com | 45DEGEXT | Briggs & Stratton Muffler Extension | $8.95
70 | 1 | SmallEngineSuppliers.com | 49M777-0853 | Briggs & Stratton 28 HP professional series | $699.95

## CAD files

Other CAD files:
cad/PC6_Control_Panel_FAB.skp
cad/PC6_Engine_Pump_Mount_FAB.skp
cad/PC6_Frame_FAB.skp
cad/PC6_Fuel_Tank_FAB.skp
cad/PC6_Hydraulic_Reservoir_FAB.skp

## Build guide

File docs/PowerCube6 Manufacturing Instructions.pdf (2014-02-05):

2/4/2014 | Power Cube 6/Manufacturing Instructions - Open Source Ecology
http://opensourceecology.org/wiki/Power_Cube_6/Manufacturing_Instructions | 1/11

# Power Cube 6/Manufacturing Instructions

From Open Source Ecology
< Power Cube 6 (http://opensourceecology.org/wiki/Power_Cube_6)

Power Cube 6
Home (http://opensourceecology.org/wiki/Power_Cube_6) | Research & Development (http://opensourceecology.org/wiki/Power_Cube_6/Research_Development) | Bill of Materials (http://opensourceecology.org/wiki/Power_Cube_6/Bill_of_Materials) | Manufacturing Instructions | User's Manual (http://opensourceecology.org/wiki/Power_Cube_6/User%27s_Manual) 78px (http://opensourceecology.org/w/index.php?title=Special:Upload&wpDestFile=Power_Cube_6.png)

Power Cube Manufacturing Instructions (http://opensourceecology.org/wiki/Power_Cube/Manufacturing_Instructions) Prepare Preparation (http://opensourceecology.org/wiki/Power_Cube/Manufacturing_Instructions#Preparation) · Safety (http://opensourceecology.org/w/index.php?action=edit&redlink=1) · Workspace (http://opensourceecology.org/w/index.php?action=edit&redlink=1) · Tools (http://opensourceecology.org/w/index.php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) · Raw Materials (http://opensourceecology.org/w/index.php?action=edit&redlink=1) · Pre-Fabricated Parts (http://opensourceecology.org/w/index.php?action=edit&redlink=1)
Subassembly
Fabrication

Engine mounts (http://opensourceecology.org/wiki/Power_Cube/Manufacturing_Instructions#Engine_mounts) · Hydraulic Pump Mount (http://opensourceecology.org/wiki/Power_Cube/Manufacturing_Instructions#Hydraulic_pump_mount) · Quick attach mounts (http://opensourceecology.org/wiki/Power_Cube/Manufacturing_Instructions#Quick_attach_mounts) · Fuel tank (http://opensourceecology.org/wiki/Power_Cube/Manufacturing_Instructions#Fuel_tank) · OilCooler Mount (http://opensourceecology.org/wiki/Power_Cube/Manufacturing_Instructions#Oil_Cooler_Mount) · Key Switches and Choke (http://opensourceecology.org/wiki/Power_Cube/Manufacturing_Instructions#Key_Switches_and_Choke) · ElectricalCables (http://opensourceecology.org/wiki/Power_Cube/Manufacturing_Instructions#Electrical_cables) · Battery Mount (http://opensourceecology.org/wiki/Power_Cube/Manufacturing_Instructions#Battery_Mount) · Hydraulic Reservoir (http://opensourceecology.org/wiki/Power_Cube/Manufacturing_Instructions#Hydraulic_reservoir)

Assembly

Frame (http://opensourceecology.org/wiki/Power_Cube/Manufacturing_Instructions#Frame) · Top / Bottom Rectangles (http://opensourceecology.org/wiki/Power_Cube/Manufacturing_Instructions#Top_.2F_Bottom_Rectangles) · Gas Tank (http://opensourceecology.org/wiki/Power_Cube/Manufacturing_Instructions#Gas_tank) · Hydraulic Tank (http://opensourceecology.org/wiki/Power_Cube/Manufacturing_Instructions#Hydraulic_tank) · Engine Mounts and Hydraulic Motor Mount (http://opensourceecology.org/wiki/Power_Cube/Manufacturing_Instructions) · Battery Mount (http://opensourceecology.org/wiki/Power_Cube/Manufacturing_Instructions#Battery_mount)
- OilCooler and Fan Mounts (http://opensourceecology.org/wiki/Power_Cube/Manufacturing_Instructions#Oil_cooler_and_fan_mounts) · Solenoid Mounting and Installation (http://opensourceecology.org/wiki/Power_Cube/Manufacturing_Instructions) · Keyswitch Brackets and Installation (http://opensourceecology.org/wiki/Power_Cube/Manufacturing_Instructions) · Choke Bracket and Installation · Throttle Adjustment (http://opensourceecology.org/wiki/Power_Cube/Manufacturing_Instructions)

## Contents

1 Overview
2 Preparation
3 SteelCut Sheet
4 Fabrication
5 Design Files
5.1 Sketchup
5.2 Electrical Diagram

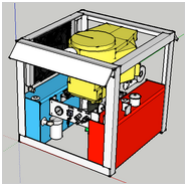
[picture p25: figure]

http://opensourceecology.org/wiki/Power_Cube_6/Manufacturing_Instructions | 2/11

PowerCube VI

5.3 Resolving Correct Labeling on Key Switch 6 Video
6.1 Subassembly Fabrication
6.2 Assembly
6.3 Final touches
6.4 See Also
6.5 Previous Versions
6.6 Peer Review

## Overview

This is the procedure for manufacturing version 6 of the OSE Power Cube.

Intro to Power Cube Construction Script (http://opensourceecology.org/wiki/Power_Cube/Intro_Video_Script)

## Preparation

1. Safety (http://opensourceecology.org/wiki/PowerCube_Safety)
2. Workspace (http://opensourceecology.org/wiki/PowerCube_Workspace)
3. Tools (http://opensourceecology.org/wiki/PowerCube_Tools)

## Steel Cut Sheet

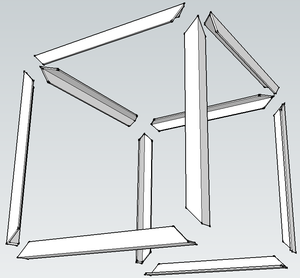
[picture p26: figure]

http://opensourceecology.org/wiki/Power_Cube_6/Manufacturing_Instructions | 3/11
Type | Cross Section | Qty | Cut Length
Flat Steel | 1/8" x 4" | 2 | 1"
Angle Iron | 1/4" x 2" x 2" | 2 | 4"
Angle Iron | 1/4" x 2" x 2" | 1 | 2"
Angle Iron* | 1/4" x 2" x 2" | 10 | 27" - 45 degree miter cuts (see diagram)
Tube - Rectangular | 1/4" x 6" x 12" | 2 | 26"
Flat Iron | 1/8" x 4" | 1 | 14"
Flat Iron | 3/8" x 4" | 2 | 26"
Flat Iron | 1/4" X 6" | 4 | 12"
Flat Iron | 1/4" X 6" | 1 | 6"
Flat Iron | 1/4" x 8" | 1 | 13.5"
Expanded Steel | 1/8" thick | 1 | 14" x 26"

Note: These angle iron pieces are to be cut at specific 45 degree angles for a mitered frame, as shown below.

http://opensourceecology.org/wiki/Power_Cube_6/Manufacturing_Instructions | 4/11

# Fabrication

# Design Files

## Sketchup

File:PC6 Fuel Tank FAB.skp (http://opensourceecology.org/wiki/File:PC6_Fuel_Tank_FAB.skp) File:PC6 Hydraulic Reservoir FAB.skp (http://opensourceecology.org/wiki/File:PC6_Hydraulic_Reservoir_FAB.skp) File:PC6 Frame FAB.skp (http://opensourceecology.org/wiki/File:PC6_Frame_FAB.skp)
File:PC6 Engine Pump Mount FAB.skp (http://opensourceecology.org/wiki/File:PC6_Engine_Pump_Mount_FAB.skp) File:PC6 Control Panel FAB.skp (http://opensourceecology.org/wiki/File:PC6_Control_Panel_FAB.skp)

## Electrical Diagram

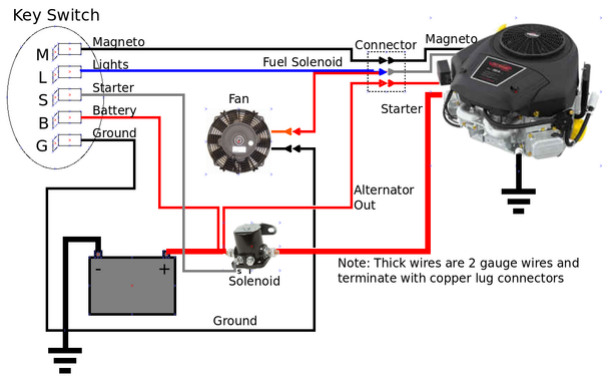
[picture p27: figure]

http://opensourceecology.org/wiki/Power_Cube_6/Manufacturing_Instructions | 5/11

From key switch:

Red - Battery Positive, Alternator Positive

Black - Battery Negative, Frame Ground

Yellow - Fuel Solenoid Positive, Fan Positive

Blue - Magneto Ground

White - Starter Solenoid Positive

## Resolving Correct Labeling on Key Switch

Note:Convention on back of key switch. M and B have different label on the metalstud - I am assuming we go by the label imprinted in the plastic.

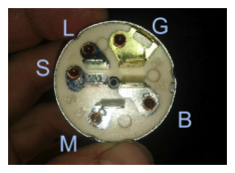
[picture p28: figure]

http://opensourceecology.org/wiki/Power_Cube_6/Manufacturing_Instructions | 6/11

edit (https://docs.google.com/drawings/d/14sKP8bw0pvIXgpXrXbzYvp6MmNKw-dqUMjk7FDI4ky4/edit)

Jack's Small Engine says:

The letters on the back of an ignition switch stand for the following:

M = Magneto
S = Starter Solenoid
L = Lights
A = Accessory
B = Battery
G = Ground
I = Ignition
R = Regulator/Rectifier

Source: http://www.jackssmallengines.com/Products/TROY-BILT/ignition-switches-keys

As for the labeling on the switch itself, we can verity with an ohmmeter:

In OFF position, M should connect to ground. In ON position, M should not connect to anything

In OFF position, B should not connect to anything. In ON position, B should connect to L

http://opensourceecology.org/wiki/Power_Cube_6/Manufacturing_Instructions | 9/11

File:Frameweld.jpg (http://opensourceecology.org/w/index.php?title=Special:Upload&wpDestFile=Frameweld.jpg)
Power Cube Frame welding

## Subassembly Fabrication

The purpose of this section is to cut the raw steel into required lengths and shapes as required for final assembly. These step includes drilling and cutting steel up to 1/4” in thickness.

1. Hydraulic Pump mount (http://opensourceecology.org/wiki/PowerCube6_Pump_Mount)
2. Fuel tank (http://opensourceecology.org/wiki/PowerCube6_Fuel_Tank)
3. Hydraulic oilreservoir (http://opensourceecology.org/wiki/PowerCube6_Hydraulic_Reservoir)
4. Control Panel (http://opensourceecology.org/w/index.php?title=PowerCube6_Control_Panel&action=edit&redlink=1)
5. Battery Mount (http://opensourceecology.org/w/index.php?title=PowerCube6_Battery_Mount&action=edit&redlink=1)

## Assembly

Power Cube assembly requires all the parts listed in the Bill Of Materials to be available and prepared as detailed in the “Fabrication” section (above). Assembly requires a welder (electric or torch) capable of welding metal 3/8” thick.

A "Stronghand" clamp has proven usefulfor 90 degree alignment of the frame members

1. Frame (http://opensourceecology.org/w/index.php?title=PowerCube6_Frame&action=edit&redlink=1)
2. Gas tank (http://opensourceecology.org/wiki/PowerCube6_Fuel_Tank)
3. Hydraulic tank (http://opensourceecology.org/w/index.php?title=PowerCube6_Hydraulic_Tank&action=edit&redlink=1)
4. Engine and Hydraulic Pump Mounts (http://opensourceecology.org/w/index.php?title=PowerCube6_Engine_Pump_Mounts&action=edit&redlink=1)
5. Battery mount (http://opensourceecology.org/w/index.php?title=PowerCube6_Battery_Mount&action=edit&redlink=1)
6. Oil cooler and fan mounts (http://opensourceecology.org/w/index.php?title=PowerCube6_Oil_Cooler_Fan_Mount&action=edit&redlink=1)
7. Solenoid Mounting Bolts (http://opensourceecology.org/w/index.php?title=PowerCube6_Solenoid_Mount&action=edit&redlink=1)
8. Throttle mount (http://opensourceecology.org/w/index.php?title=PowerCube6_Throttle_Mount&action=edit&redlink=1)
9. Keyswitch mount (http://opensourceecology.org/w/index.php?title=PowerCube6_Keyswitch_Mount&action=edit&redlink=1)
10. Quick Attach Plates (http://opensourceecology.org/w/index.php?title=PowerCube6_Quick_Attac_Plates&action=edit&redlink=1)
11. Painting (http://opensourceecology.org/w/index.php?title=PowerCube6_Painting&action=edit&redlink=1)
12. Install Hydraulic Components (http://opensourceecology.org/w/index.php?title=PowerCube6_Install_Hydraulics&action=edit&redlink=1)
13. Install Engine and Pump (http://opensourceecology.org/w/index.php?title=PowerCube6_Install_Engine_Pump&action=edit&redlink=1)
14. Install Solenoid (http://opensourceecology.org/w/index.php?title=PowerCube6_Install_Solenoid&action=edit&redlink=1)
15. Install Muffler (http://opensourceecology.org/w/index.php?title=PowerCube6_Install_Muffler&action=edit&redlink=1)

http://opensourceecology.org/wiki/Power_Cube_6/Manufacturing_Instructions | 10/11
16. Wiring (http://opensourceecology.org/w/index.php?title=PowerCube6_Wiring&action=edit&redlink=1)
17. Install Throttle Control (http://opensourceecology.org/w/index.php?title=PowerCube6_Throttle&action=edit&redlink=1)

## Final touches

1. Install engine and secure with bolts, nuts and washers
2. Connect wiring to key switch and solenoid
3. Connect fuel line
4. Connect coupling to engine shaft
5. Install hydraulic pump on coupling and secure with nuts & washers
6. Installfan and hydraulic oil cooler

## See Also

See also Power_Cube_Fabrication_Procedure (http://opensourceecology.org/wiki/Power_Cube_Fabrication_Procedure) for older model.

Work in progress by Tom Griffing - File:Powercube.odt (http://opensourceecology.org/wiki/File:Powercube.odt)File:Powercube.pdf (http://opensourceecology.org/wiki/File:Powercube.pdf)

File:PowerCube.skp (http://opensourceecology.org/wiki/File:PowerCube.skp)

## Previous Versions

Power Cube Fabrication June 2011 (http://opensourceecology.org/wiki/Power_Cube/Manufacturing_Instructions/Fabrication_June_2011)

## Peer Review

I would do double chain coupler. I have had good experience with it - it will extend pump life because it will eliinate any strain on the pump shaft, while easing accuracy requirements for pump mount welding.

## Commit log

2014-01-29 git import
    [PcVIcontrol.skp, controlpanel.scad, controlpanel.stl]
2014-01-29 additional Tom Griffing contributions
    [PC6_Control_Panel_FAB.skp, PC6_Engine_Pump_Mount_FAB.skp, PC6_Frame_FAB.skp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]
2014-01-29 rearrange for clarity
    [PcVIcontrol.skp]
2014-02-04 move cad files around
    [PC6_Control_Panel_FAB.skp, PC6_Engine_Pump_Mount_FAB.skp, PC6_Frame_FAB.skp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]
2014-02-04 add bom
    [bom.csv]
2014-02-05 remove header for readability
    [bom.csv]
2014-02-05 add hyperlink removed from bom.csv
2014-02-24 uncompress cad; delete v7 drawings
